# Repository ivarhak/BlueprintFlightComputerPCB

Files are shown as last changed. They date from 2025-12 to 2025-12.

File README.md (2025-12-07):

Files for my flight computer project as a part of the Hack Club foundation's Blueprint program 2025.
Board has an STM chip, 2 BMP351 barometers, 1 ICM-42688-P IMU, a microSD slot, battery charging capabilities, and servo pins.
Feel free to use and modify.

The main idea with the board is to have a solid platform on which there are high-quality sensors to put on any rocketry project. The two barometers help eliminate noise, and the ICM is of high quality. The two servo pin headers let the user connect this flight computer to any PWM project, like airbrakes or canard systems. 

Special thanks to @Notaroomba, Hack Club, and @rasmushauschild for creating the guides and tools necessary to make this awesome PCB.
3d model can be found in the hardware folder, was so big I had to compress it.







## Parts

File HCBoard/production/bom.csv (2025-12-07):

Designator | Footprint | Quantity | Value | LCSC Part #
C1, C11, C2, C24, C43, C5, C7, C8, C9 | C0805 | 9 | CL21A106KAYNNNE | C15850
C10, C17, C20, C21, C22, C23, C27, C28, C29, C30, C31, C37, C42 | 0201 | 13 | CL10A105KB8NNNC | C14663
C12, C13, C14, C25, C3, C4, C6 | C0805 | 7 | CL21A226MAYNNNE | C602037
C15, C16, C26, C38, C39, C40, C41 | 0201 | 7 | CL10A105KB8NNNC | C15849
C18, C19 | 0805 | 2 | CL21A226MAYNNNE | C602037
C32 | C0603 | 1 | CL10A225KO8NNNC | C23630
C33, C34 | C0603 | 2 | CL10C200JB8NNNC | C1648
C35, C36 | C0603 | 2 | 0603CG6R8C500NT | C1679
CARD1 | TF-SMD_TF-01A | 1 | TF-01A | C91145
H1, H2 | HDR-TH_3P-P2.54-V-M-1 | 2 | HX PH254-01-03-Z-L11.5 PCB PIN HEADER | C52016391
L1, L2 | 1008 | 2 | 1.5uH
L3 | L_Changjiang_FXL0630 | 1 | 5.6uH
L4 | L0603 | 1 | FCM1608KF-601T03 | C141723
LED1 | LED0603-FD | 1 | YLED0603R | C19171390
R1, R2 | R0603 | 2 | FRC0603F5101TS | C2907044
R10 | 0402 | 1 | 383
R12, R13, R24, R25, R26, R27, R28, R29, R3, R30, R4, R5, R7 | R0603 | 13 | RC0603FR-0710KL | C98220
R14, R8 | 0201 | 2 | 100K
R15 | 0201 | 1 | 22K
R16, R17, R18, R19, R31, R32, R6 | R0805 | 7 | 0805W8F2201T5E | C17520
SW1, SW2 | SW-SMD_L3.9-W3.0-P4.45 | 2 | TS-1088-AR02016 | C720477
U1 | VQFN-HR-15_L3.0-W2.5-P0.50-BL_TPS63070RNMR | 1 | TPS63070RNMR | C109322
U2 | WQFN-24_L4.0-W4.0-P0.50-TL-EP2.7 | 1 | BQ25895MRTWR | C485917
U3, U8 | LGA-10_L2.0-W2.0-P0.50-TL_BMP581 | 2 | BMP581 | C5362283
U5 | SOT-23-6_L2.9-W1.6-P0.95-LS2.8-BL | 1 | LMR51430XDDCR | C5185863
U6 | LQFP-64_L10.0-W10.0-P0.50-LS12.0-BL | 1 | STM32F722RET6 | C118207
U7 | CONN-TH_DB301V-3.5-2P-GN | 1 | DB301V-3.5-2P-GN | C695629
U9 | LGA-14_L3.0-W2.5-P0.50-TL | 1 | ICM-42688-P | C1850418
USB1 | USB-C-SMD_TYPE-C-6PIN-2MD-073 | 1 | TYPE-C 16PIN 2MD(073) | C2765186
X1 | CRYSTAL-SMD_4P-L3.2-W2.5-BL | 1 | X322525MOB4SI | C9006
X2 | FC-135R_L3.2-W1.5 | 1 | Q13FC1350000400 | C32346

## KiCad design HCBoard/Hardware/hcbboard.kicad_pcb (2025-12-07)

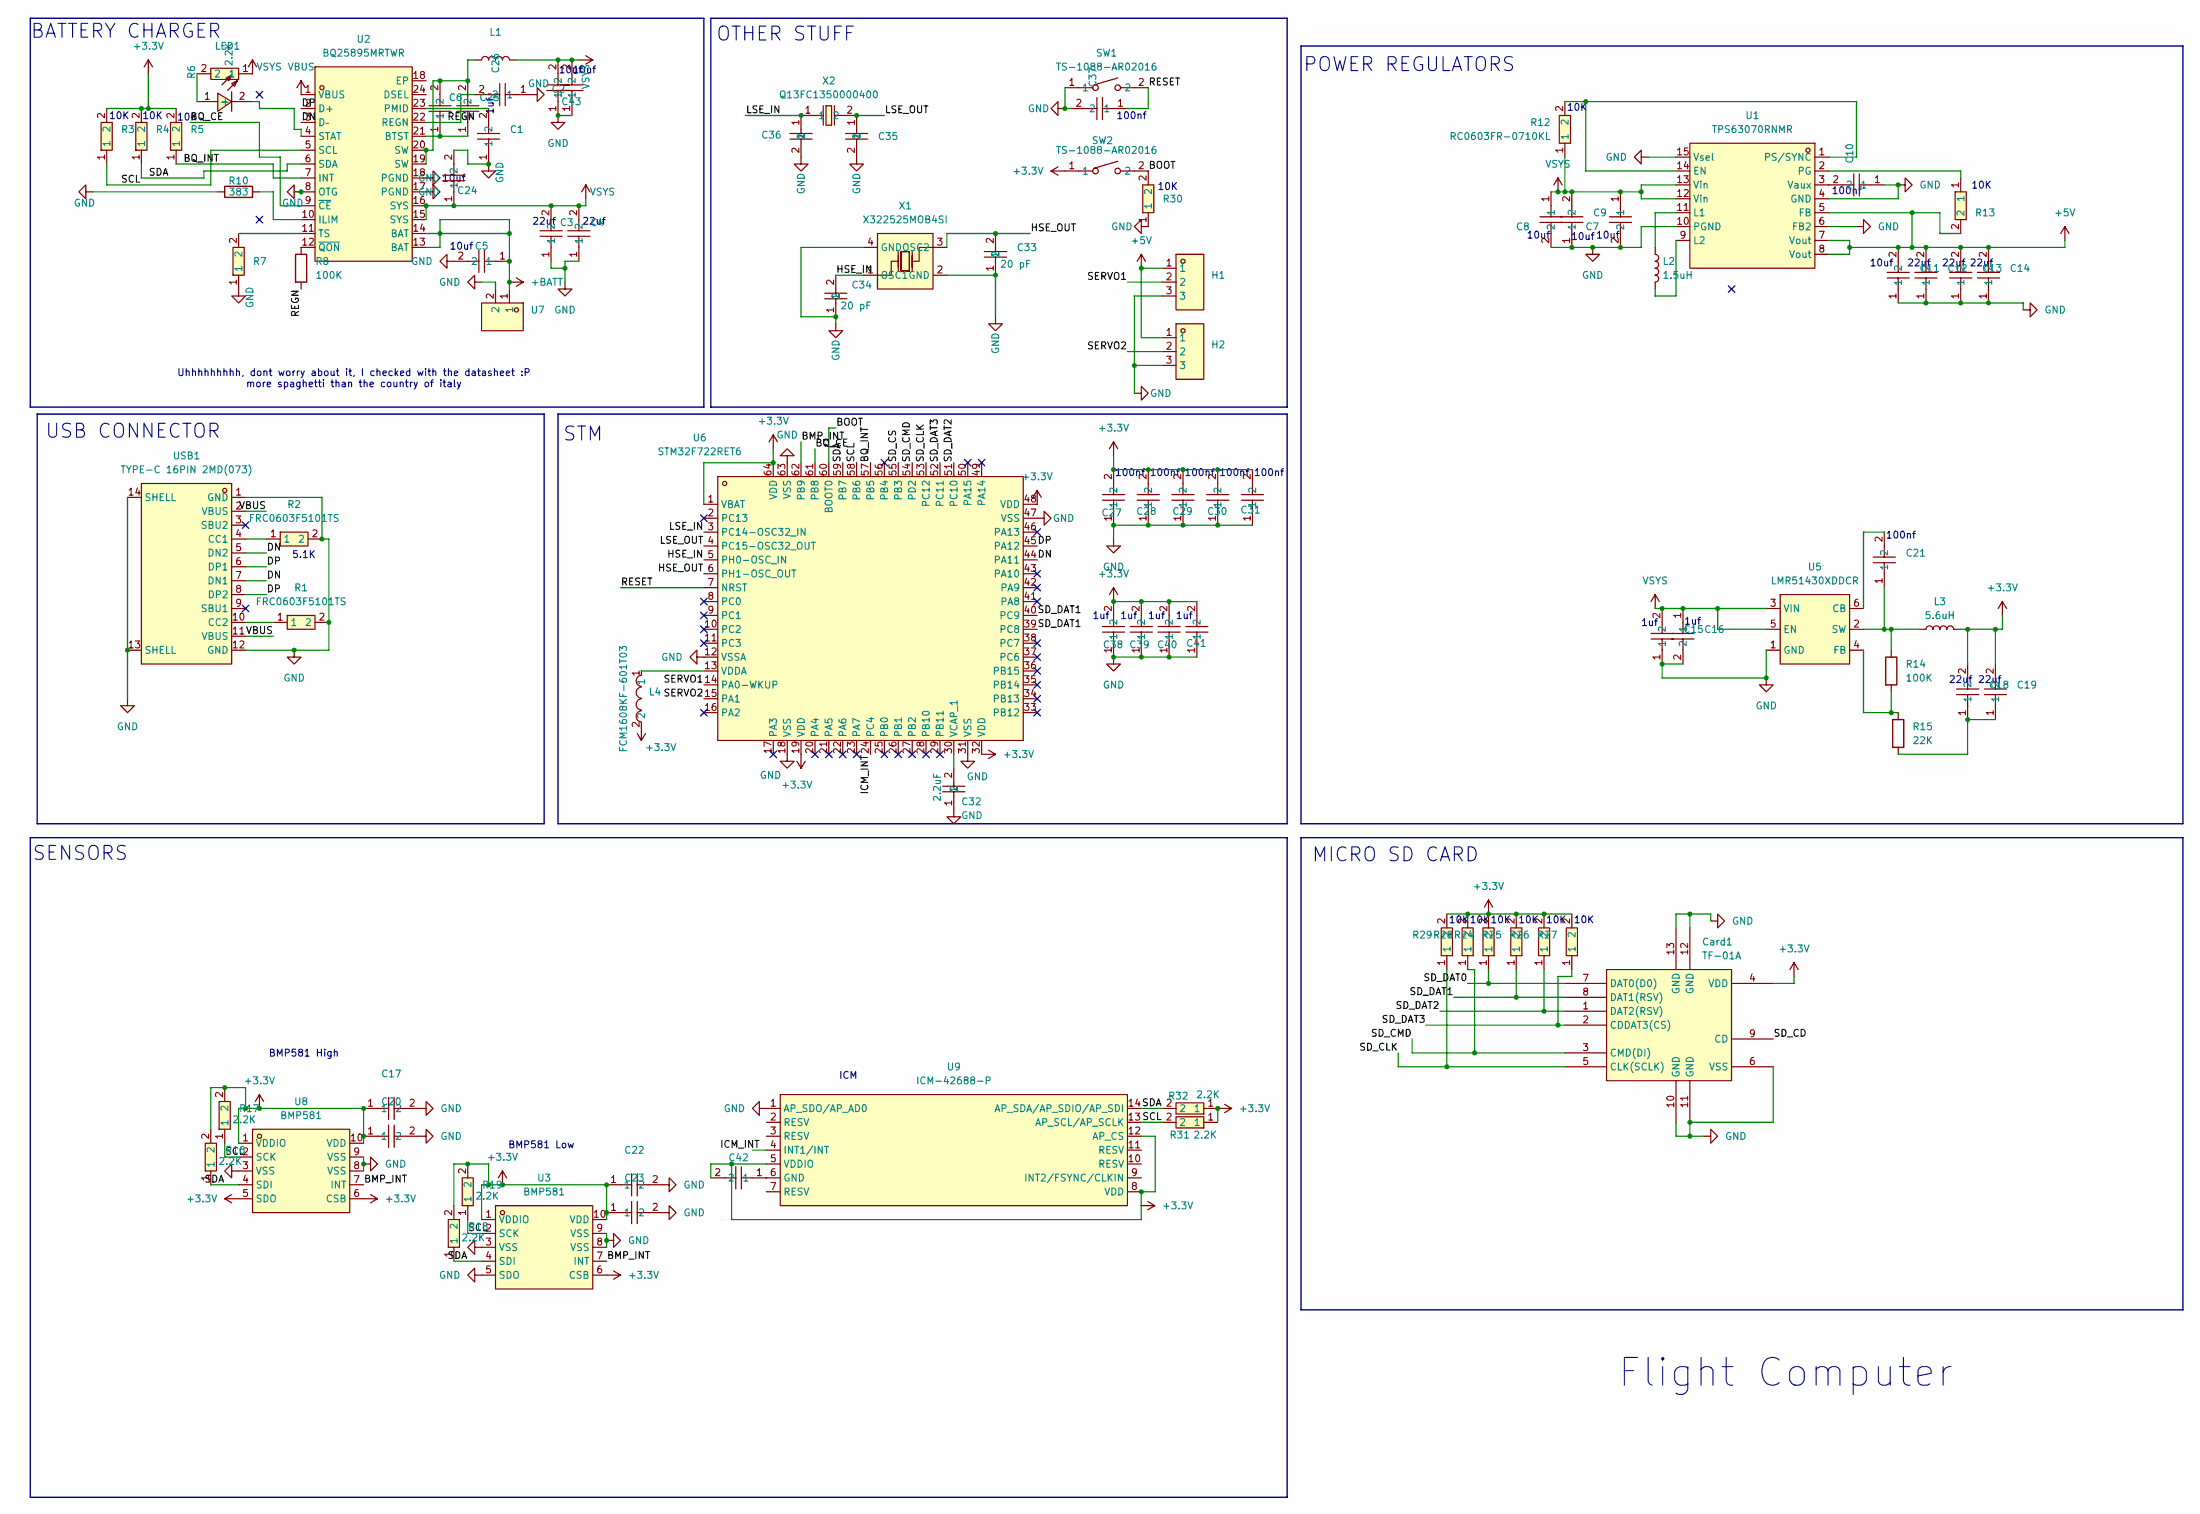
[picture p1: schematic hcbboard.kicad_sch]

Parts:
C1, C2, C5, C7, C8, C9, C11, C24, C43: CL21A106KAYNNNE; C0805; LCSC Part C15850
C3, C4, C6, C12, C13, C14, C25: CL21A226MAYNNNE; C0805; LCSC Part C602037
C10, C17, C20, C21, C22, C23, C27, C28, C29, C30, C31, C37, C42: CL10A105KB8NNNC; C_0201_0603Metric; LCSC Part C14663
C15, C16, C26, C38, C39, C40, C41: CL10A105KB8NNNC; C_0201_0603Metric; LCSC Part C15849
C18, C19: CL21A226MAYNNNE; C_0805_2012Metric; LCSC Part C602037
C32: CL10A225KO8NNNC; C0603; LCSC Part C23630
C33, C34: CL10C200JB8NNNC; C0603; LCSC Part C1648
C35, C36: 0603CG6R8C500NT; C0603; LCSC Part C1679
Card1: TF-01A; TF-SMD_TF-01A; LCSC Part C91145
H1, H2: HX PH254-01-03-Z-L11.5 PCB PIN HEADER; HDR-TH_3P-P2.54-V-M-1; LCSC Part C52016391
L1, L2: 1.5uH; L_1008_2520Metric
L3: 5.6uH; L_Changjiang_FXL0630
L4: FCM1608KF-601T03; L0603; LCSC Part C141723
LED1: YLED0603R; LED0603-FD; LCSC Part C19171390
R1, R2: FRC0603F5101TS; R0603; LCSC Part C2907044
R3, R4, R5, R7, R12, R13, R24, R25, R26, R27, R28, R29, R30: RC0603FR-0710KL; R0603; LCSC Part C98220
R6, R16, R17, R18, R19, R31, R32: 0805W8F2201T5E; R0805; LCSC Part C17520
R8, R14: 100K; R_0201_0603Metric
R10: 383; C_0402_1005Metric
R15: 22K; R_0201_0603Metric
SW1, SW2: TS-1088-AR02016; SW-SMD_L3.9-W3.0-P4.45; LCSC Part C720477
U1: TPS63070RNMR; VQFN-HR-15_L3.0-W2.5-P0.50-BL_TPS63070RNMR; LCSC Part C109322
U2: BQ25895MRTWR; WQFN-24_L4.0-W4.0-P0.50-TL-EP2.7; LCSC Part C485917
U3, U8: BMP581; LGA-10_L2.0-W2.0-P0.50-TL_BMP581; LCSC Part C5362283
U5: LMR51430XDDCR; SOT-23-6_L2.9-W1.6-P0.95-LS2.8-BL; LCSC Part C5185863
U6: STM32F722RET6; LQFP-64_L10.0-W10.0-P0.50-LS12.0-BL; LCSC Part C118207
U7: DB301V-3.5-2P-GN; CONN-TH_DB301V-3.5-2P-GN; LCSC Part C695629
U9: ICM-42688-P; LGA-14_L3.0-W2.5-P0.50-TL; LCSC Part C1850418
USB1: TYPE-C 16PIN 2MD(073); USB-C-SMD_TYPE-C-6PIN-2MD-073; LCSC Part C2765186
X1: X322525MOB4SI; CRYSTAL-SMD_4P-L3.2-W2.5-BL; LCSC Part C9006
X2: Q13FC1350000400; FC-135R_L3.2-W1.5; LCSC Part C32346

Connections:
+3.3V: C17.1, C18.2, C19.2, C20.1, C22.1, C23.1, C27.2, C28.2, C29.2, C30.2, C31.2, C38.2, C39.2, C40.2, C41.2, Card1.4 (VDD), L3.2, L4.2, R3.2, R4.2, R5.2, R16.2, R17.2, R18.2, R19.2, R24.2, R25.2, R26.2, R27.2, R28.2, R29.2, R31.1, R32.1, SW2.1, U3.1 (VDDIO), U3.6 (CSB), U3.10 (VDD), U6.1 (VBAT), U6.19 (VDD), U6.32 (VDD), U6.48 (VDD), U6.64 (VDD), U8.1 (VDDIO), U8.5 (SDO), U8.6 (CSB), U8.10 (VDD)
+5V: C11.2, C12.2, C13.2, C14.2, H1.1, H2.1, R13.2, U1.5 (FB), U1.7 (Vout), U1.8 (Vout)
+BATT: C5.1, U2.13 (BAT), U2.14 (BAT), U7.1
/BMP_INT: U3.7 (INT), U6.62 (PB9), U8.7 (INT)
/BOOT: R30.2, SW2.2, U6.60 (BOOT0)
/BQ_CE: U2.9 (~CE), U6.61 (PB8)
/BQ_INT: R5.1, U2.7 (INT), U6.57 (PB5)
/DP: U2.2 (D+), U6.45 (PA12), USB1.6 (DP1), USB1.8 (DP2)
/HSE_IN: C34.2, U6.5 (PH0-OSC_IN), X1.1 (OSC1)
/HSE_OUT: C33.2, U6.6 (PH1-OSC_OUT), X1.3 (OSC2)
/ICM_INT: U6.24 (PC4), U9.4 (INT1/INT)
/LSE_IN: C36.1, U6.3 (PC14-OSC32_IN), X2.1
/LSE_OUT: C35.1, U6.4 (PC15-OSC32_OUT), X2.2
/REGN: C26.2, R8.2, U2.22 (REGN)
/RESET: C37.1, SW1.2, U6.7 (NRST)
/SCL: R3.1, R17.1, R19.1, R31.2, U2.5 (SCL), U3.2 (SCK), U6.58 (PB6), U8.2 (SCK), U9.13 (AP_SCL/AP_SCLK)
/SDA: R4.1, R16.1, R18.1, R32.2, U2.6 (SDA), U3.4 (SDI), U6.59 (PB7), U8.4 (SDI), U9.14 (AP_SDA/AP_SDIO/AP_SDI)
/SD_CD: Card1.9 (CD)
/SD_CLK: Card1.5 (CLK(SCLK)), R29.1, U6.53 (PC12)
/SD_CMD: Card1.3 (CMD(DI)), R28.1, U6.54 (PD2)
/SD_CS: U6.55 (PB3)
/SD_DAT0: Card1.7 (DAT0(D0)), R24.1
/SD_DAT1: Card1.8 (DAT1(RSV)), R25.1, U6.39 (PC8), U6.40 (PC9)
/SD_DAT2: Card1.1 (DAT2(RSV)), R26.1, U6.51 (PC10)
/SD_DAT3: Card1.2 (CDDAT3(CS)), R27.1, U6.52 (PC11)
/SERVO1: H1.2, U6.14 (PA0-WKUP)
/SERVO2: H2.2, U6.15 (PA1)
GND: C1.1, C2.1, C3.1, C4.1, C5.2, C7.2, C8.2, C9.1, C10.1, C11.1, C12.1, C13.1, C14.1, C15.1, C16.2, C17.2, C20.2, C22.2, C23.2, C24.2, C26.1, C27.1, C28.1, C29.1, C30.1, C31.1, C32.1, C33.1, C34.1, C35.2, C36.2, C37.2, C38.1, C39.1, C40.1, C41.1, C43.1, Card1.6 (VSS), Card1.10 (GND), Card1.11 (GND), Card1.12 (GND), Card1.13 (GND), H1.3, H2.3, R1.2, R2.2, R7.1, R10.1, R30.1, SW1.1, U1.4 (GND), U1.6 (FB2), U1.10 (PGND), U1.15 (Vsel), U2.8 (OTG), U2.17 (PGND), U2.18 (PGND), U3.3 (VSS), U3.5 (SDO), U3.8 (VSS), U3.9 (VSS), U5.1 (GND), U6.12 (VSSA), U6.18 (VSS), U6.31 (VSS), U6.47 (VSS), U6.63 (VSS), U7.2, U8.3 (VSS), U8.8 (VSS), U8.9 (VSS), U9.1 (AP_SDO/AP_AD0), USB1.1 (GND), USB1.12 (GND), USB1.13 (SHELL), USB1.14 (SHELL), X1.2 (GND), X1.4 (GND)
unnamed: C18.1, C19.1, R15.2
unnamed: C6.2, C25.2, L1.1, U2.19 (SW), U2.20 (SW)
unnamed: LED1.1 (+), R6.2
unnamed: LED1.2 (-), U2.4 (STAT)
unnamed: R12.2, U1.1 (PS/SYNC), U1.14 (EN)
unnamed: L2.1, U1.11 (L1)
unnamed: L2.2, U1.9 (L2)
unnamed: R13.1, U1.2 (PG)
unnamed: C10.2, U1.3 (Vaux)
unnamed: C6.1, C25.1, U2.21 (BTST)
unnamed: R10.2, U2.10 (ILIM)
unnamed: C1.2, U2.23 (PMID)
unnamed: R7.2, U2.11 (TS)
unnamed: R8.1, U2.12 (~QON)
unnamed: C21.2, U5.6 (CB)
unnamed: R14.2, R15.1, U5.4 (FB)
unnamed: C21.1, L3.1, R14.1, U5.2 (SW)
unnamed: C32.2, U6.30 (VCAP_1)
unnamed: L4.1, U6.13 (VDDA)
unnamed: C42.2, U9.5 (VDDIO), U9.8 (VDD), U9.12 (AP_CS)
unnamed: C42.1, U9.6 (GND)
unnamed: R2.1, USB1.4 (CC1)
unnamed: R1.1, USB1.10 (CC2)
VSYS: C2.2, C3.2, C4.2, C7.1, C8.1, C9.2, C15.2, C16.1, C24.1, C43.2, L1.2, R6.1, R12.1, U1.12 (Vin), U1.13 (Vin), U2.15 (SYS), U2.16 (SYS), U5.3 (VIN), U5.5 (EN)

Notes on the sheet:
1uf
22uf
10uf
10K
5.1K
POWER REGULATORS
100nf
BATTERY CHARGER
ICM
USB CONNECTOR
STM
OTHER STUFF
SENSORS
MICRO SD CARD
BMP581 Low
Uhhhhhhhhh, dont worry about it, I checked with the datasheet :P more spaghetti than the country of italy
Flight Computer
BMP581 High

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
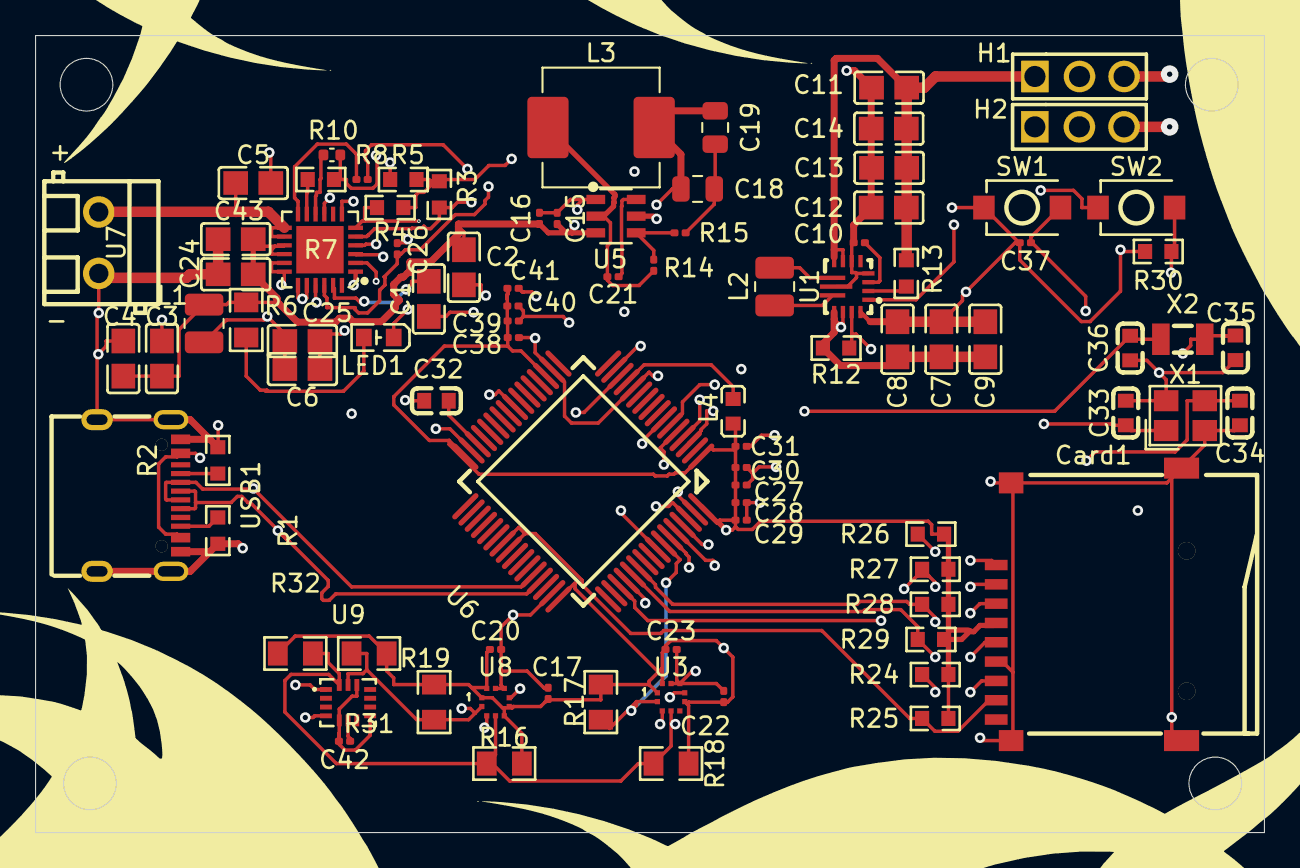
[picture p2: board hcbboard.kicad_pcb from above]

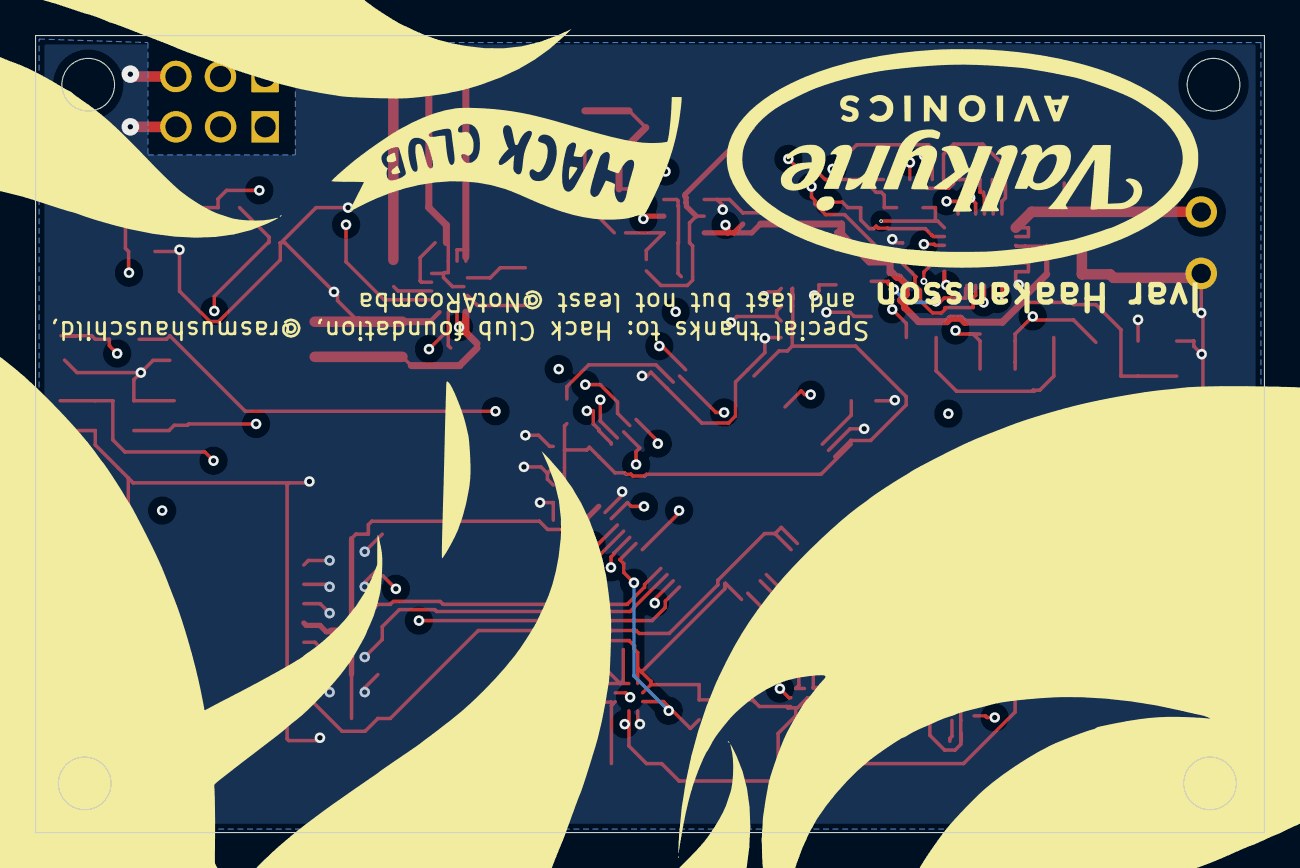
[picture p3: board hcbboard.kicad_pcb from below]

Board: 4 copper layers, 70.0 x 45.4 mm, 106 parts (7 on the bottom side), 52 nets.

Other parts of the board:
6765765: LOGO
G1313, G12414, G42414, G54353, G67567, G112323, G0202002, G321213, G424124, G546546, G567567, G756657, G757657, G2423423, G45345435: LOGO

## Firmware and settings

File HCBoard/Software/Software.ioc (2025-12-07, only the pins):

Mcu.UserName=STM32F722RETx
PA0-WKUP.Signal=S_TIM2_CH1_ETR
PA1.Signal=S_TIM2_CH2
PA11.Signal=USB_OTG_FS_DM
PA12.Signal=USB_OTG_FS_DP
PA4.Signal=SPI1_NSS
PA5.Signal=SPI1_SCK
PA6.Signal=SPI1_MISO
PA7.Signal=SPI1_MOSI
PB3.GPIO_Label=SD_CS
PB3.Signal=GPIO_Input
PB5.GPIO_Label=BQ_INT
PB5.Signal=GPXTI5
PB6.Signal=I2C1_SCL
PB7.Signal=I2C1_SDA
PB8.GPIO_Label=BQ_CE
PB8.Signal=GPIO_Output
PB9.GPIO_Label=BMP_INT
PB9.Signal=GPXTI9
PC10.Signal=SDMMC1_D2
PC11.Signal=SDMMC1_D3
PC12.Signal=SDMMC1_CK
PC14-OSC32_IN.Signal=RCC_OSC32_IN
PC15-OSC32_OUT.Signal=RCC_OSC32_OUT
PC4.GPIO_Label=ICM_INT1
PC4.Signal=GPXTI4
PC8.Signal=SDMMC1_D0
PC9.Signal=SDMMC1_D1
PD2.Signal=SDMMC1_CMD
PH0-OSC_IN.Signal=RCC_OSC_IN
PH1-OSC_OUT.Signal=RCC_OSC_OUT
